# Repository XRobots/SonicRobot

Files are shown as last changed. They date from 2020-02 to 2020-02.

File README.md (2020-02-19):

# SonicRobot

Code and CAD for my two-wheel balancing robot:  https://www.youtube.com/playlist?list=PLpwJoq86vov_tZ3rsMCH5sylqGT5s9TcU

Main parts in the robot are (more details in part 2 of the video series).

-Teensy 3.6 for the main processor.

-MPU6050 on a GY521 style breakout.

-2x Teensy 3.2 to read the load cells in the legs.

-2x 20Kg Loadcells.

-2x Sparkfun Qwiic Scales: https://www.sparkfun.com/products/15242 .

-'SN65HVD230 CAN BusBoard Network Transceiver Module compatible with PCA82C250' CAN Bus Trancievers.

-2x ODrive 3.6 56V version.

-2x 150Kv 6374 ODrive branded brushless motors.

-2x Turnigy SK3 6374 149Kv brushless motors.

-4x 8192 CPR encoders also availabe from ODrive.

-Some switches etc to initialise the Odrives and an Estop which brings the ODrive RST pins to ground.

-NRF24L01 Rf device.

-Varios proto board.

Main parts in the remote are:

-Arduino MEGA2650.

-Another NRF24L01 RF device.

-some switches, and some 3-axis joysticks I got from eBay.

Other mechanical parts (check part 1 for  more details):

-2x Wheel drive belts - 450mm AT5 belts.

-2x Wheel drive motor pulleys - 14 tooth AT5 aluminium pulleys, 8mm bore to match the motors.

-2x 200mm SFU1605 ball screws

-2x 10mm-10mm CNC couplers

-8x CNC style V-Wheels, 5mm ID bearings, plus nuts and bolts.

-4x M10/10mm Rose joints.

-A bunch of 2040 and 2020 Vslot extrusion - refer to the CAD and video.

-Misc T-nuts and M4 bolts of various lengths.

-8x 12mm ID / 32mm OD / 10mm thick bearings for hip joints.

-8x 8mm ID / 22mm OD / 7mm thick bearings for knee joints.

-Various lengths of M12 and M10 studding plus washers and nuts to suit.

Other details:

-I'm running it off 2x 6S 5000 mAH LiPo packs in series

-Electronics are on a separate 5v regulator running from a separate 11.1v LiPo battery.

-Put 0.1uF decoupling capacitors on everything.

Main Library Dependencies are:

For Teensy CAN: https://github.com/tonton81/IFCT

For the MPU 6050: https://github.com/jrowberg/i2cdevlib

For the load cells: https://github.com/sparkfun/SparkFun_Qwiic_Scale_NAU7802_Arduino_Library/

For the ODrvies: https://github.com/madcowswe/ODrive/tree/master/Arduino/ODriveArduino

Plus RF24 library from the Arduino libraries manager, other built in libraries

Use the IMUzero example included with the MPU6050 to read the IMU calibration setting and put those into your sketch: https://github.com/jrowberg/i2cdevlib/tree/master/Arduino/MPU6050/examples/IMU_Zero

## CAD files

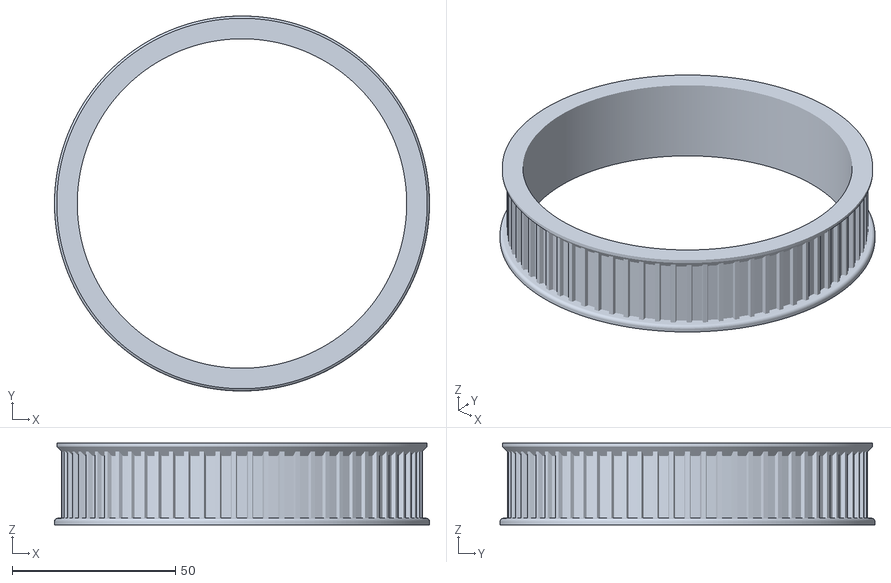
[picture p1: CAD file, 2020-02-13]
CAD/WheelPulley.stl
115.0 x 115.0 x 25.0

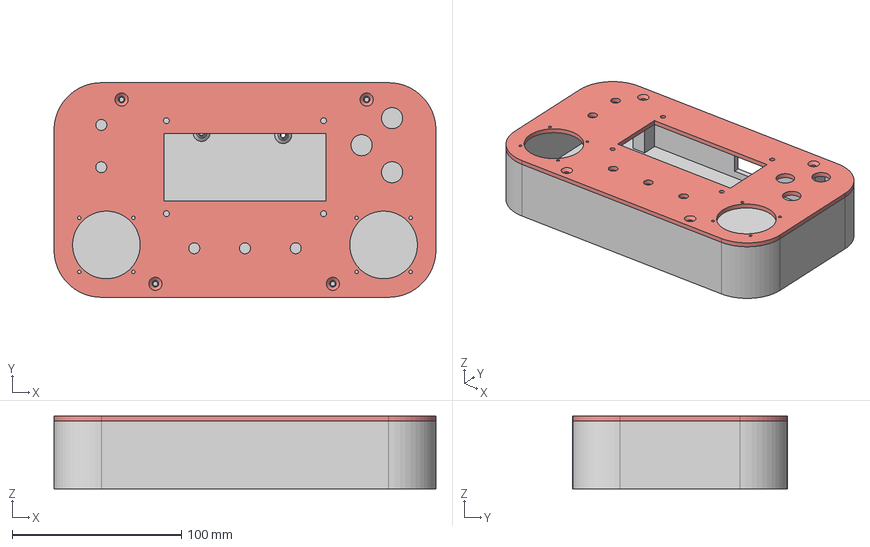
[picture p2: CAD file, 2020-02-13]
CAD/Remote.stp
226.0 x 127.0 x 43.0 mm

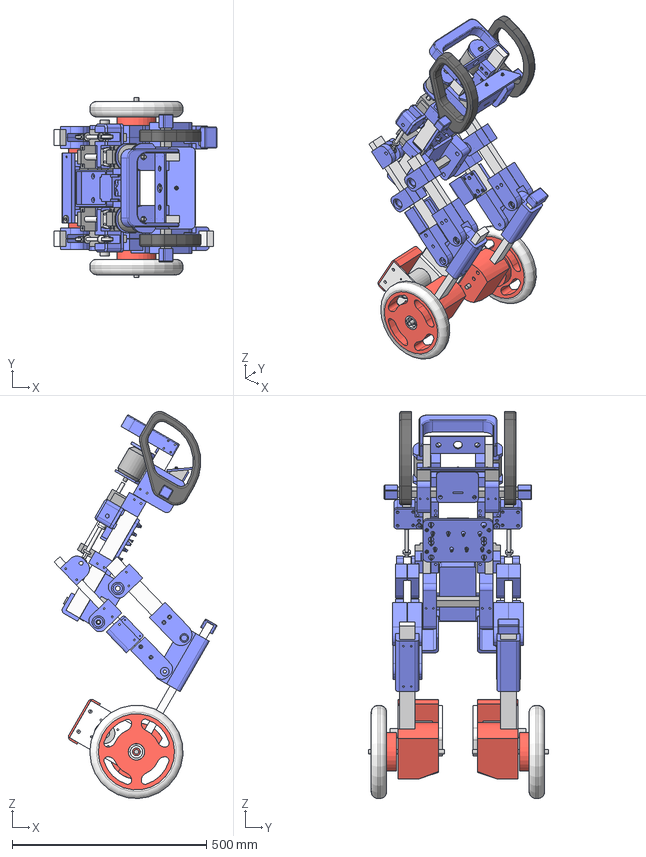
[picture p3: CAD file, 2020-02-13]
CAD/Sonic05.stp
418.0 x 463.0 x 995.0 mm
shin
thigh (1)
thigh (1) (1)
shin(Mirror)
thigh (1)(Mirror)
thigh (1) (1)(Mirror)
ballNut
ballNut (1)
rosejoint(Mirror)
rosejoint(Mirror)(Mirror)

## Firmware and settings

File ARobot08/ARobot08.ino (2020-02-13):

#include <SPI.h>
#include <nRF24L01.h>
#include <RF24.h>
#include <PID_v1.h>  //PID loop from http://playground.arduino.cc/Code/PIDLibrary
#include <Servo.h>
#include <IFCT.h>

Servo servo1;
Servo servo2;

double Pk1 = 7500;          // balancing PID
double Ik1 = 75000;
double Dk1 = 180;

double Setpoint1, Input1, Output1;    // PID variables
PID PID1(&Input1, &Output1, &Setpoint1, Pk1, Ik1 , Dk1, DIRECT);    // PID Setup - balancing IMU

double Pk2 = 3;          // Side to Side PID
double Ik2 = 0;
double Dk2 = 0;

double Setpoint2, Input2, Output2;    // PID variables
PID PID2(&Input2, &Output2, &Setpoint2, Pk2, Ik2 , Dk2, DIRECT);    // PID Setup - side to side IMU

double Pk3 = 22;          // load cell PID
double Ik3 = 0;
double Dk3 = 0;

double Setpoint3, Input3, Output3;    // PID variables
PID PID3(&Input3, &Output3, &Setpoint3, Pk3, Ik3 , Dk3, DIRECT);    // PID Setup - load cell 1

double Pk4 = 22;          // load cell PID
double Ik4 = 0;
double Dk4 = 0;

double Setpoint4, Input4, Output4;    // PID variables
PID PID4(&Input4, &Output4, &Setpoint4, Pk4, Ik4 , Dk4, DIRECT);    // PID Setup - loadcell 2

RF24 radio(25, 24); // CE, CSN
const byte addresses[][6] = {"00001", "00002"};

#include "I2Cdev.h"
#include "MPU6050_6Axis_MotionApps20.h"
#include "Wire.h"
#include <ODriveArduino.h>

// Printing with stream operator
template<class T> inline Print& operator <<(Print &obj,     T arg) { obj.print(arg);    return obj; }
template<>        inline Print& operator <<(Print &obj, float arg) { obj.print(arg, 4); return obj; }

//ODrive Object
ODriveArduino odrive(Serial2);
ODriveArduino odrive2(Serial3);

//**************remote control****************
struct RECEIVE_DATA_STRUCTURE{
  //put your variable definitions here for the data you want to send
  //THIS MUST BE EXACTLY THE SAME ON THE OTHER ARDUINO 

    int16_t menuDown;      
    int16_t Select; 
    int16_t menuUp;  
    int16_t toggleBottom;  
    int16_t toggleTop; 
    int16_t toggle1; 
    int16_t toggle2; 
    int16_t mode;  
    int16_t RLR;
    int16_t RFB;
    int16_t RT;
    int16_t LLR;
    int16_t LFB;
    int16_t LT;
    int16_t checkit;
    int16_t checkit2;

};

int stickRFB;
int stickRLR;
int stickLLR;
int toggleTop;
int toggleBottom;

RECEIVE_DATA_STRUCTURE mydata_remote;

int requested_state;   

// class default I2C address is 0x68
// specific I2C addresses may be passed as a parameter here
// AD0 low = 0x68 (default for SparkFun breakout and InvenSense evaluation board)
// AD0 high = 0x69
MPU6050 mpu;
//MPU6050 mpu(0x69); // <-- use for AD0 high

#define LED_PIN 13 // (Arduino is 11, Teensy is 11, Teensy++ is 6)
bool blinkState = false;

// MPU control/status vars
bool dmpReady = false;  // set true if DMP init was successful
uint8_t mpuIntStatus;   // holds actual interrupt status byte from MPU
uint8_t devStatus;      // return status after each device operation (0 = success, !0 = error)
uint16_t packetSize;    // expected DMP packet size (default is 42 bytes)
uint16_t fifoCount;     // count of all bytes currently in FIFO
uint8_t fifoBuffer[64]; // FIFO storage buffer

// orientation/motion vars
Quaternion q;           // [w, x, y, z]         quaternion container
VectorInt16 aa;         // [x, y, z]            accel sensor measurements
VectorInt16 aaReal;     // [x, y, z]            gravity-free accel sensor measurements
VectorInt16 aaWorld;    // [x, y, z]            world-frame accel sensor measurements
VectorFloat gravity;    // [x, y, z]            gravity vector
float euler[3];         // [psi, theta, phi]    Euler angle container
float ypr[3];           // [yaw, pitch, roll]   yaw/pitch/roll container and gravity vector


float pitch;
float roll;
long velocity;

int menuFlag = 0;
float SetpointTrim1 = 0;

float accum = 0;
float accum2 = 0;
float outputDiv;

float trimPot;
float trimAngle;

float RFB;
int RLR;
int LT;
int LLR;

long drive1;
long drive2;

int switch1;
int switch2;

int toggle1;
int toggle2;

float leg1Dyn;
float leg2Dyn;
float leg1;
float leg2;
float leg1Filtered;
float leg2Filtered;

float leg3;
float leg4;
float leg3Filtered;
float leg4Filtered;

float leg1Output;
float leg2Output;

float legs;
float legs2;

float arm1;
float arm2;

float arm1Filtered;
float arm2Filtered;

unsigned long currentMillis;

long previousMillis = 0;    // set up timers
long interval = 10;        // time constant for timers
unsigned long count;

int loopTime;
int previousLooptime;

unsigned long previousSafetyMillis;

int IMUdataReady = 0;
volatile bool mpuInterrupt = false;     // indicates whether MPU interrupt pin has gone high

int bitVar1;    // CAN bus receive
int bitVar2;
int bitVar1Z = 0;    // CAN bus receive
int bitVar2Z = 0;

// ****************** SETUP ******************************

void setup() {

    // radio stuff

    radio.begin();
    radio.openWritingPipe(addresses[0]); // 00002
    radio.openReadingPipe(1, addresses[1]); // 00001
    radio.setPALevel(RF24_PA_MIN);

    radio.startListening();
    
    // join I2C bus (I2Cdev library doesn't do this automatically)
    #if I2CDEV_IMPLEMENTATION == I2CDEV_ARDUINO_WIRE
        Wire.begin();
        Wire.setClock(100000); // 400kHz I2C clock. Comment this line if having compilation difficulties
    #elif I2CDEV_IMPLEMENTATION == I2CDEV_BUILTIN_FASTWIRE
        Fastwire::setup(400, true);
    #endif

    // initialize serial communication
    Serial.begin(115200);

    //ODrive serial port
    Serial2.begin(115200);
    Serial3.begin(115200);

    // initialize IMU 
    mpu.initialize();
    devStatus = mpu.dmpInitialize();

    // supply your own gyro offsets here, scaled for min sensitivity
    mpu.setXGyroOffset(176);
    mpu.setYGyroOffset(-31);
    mpu.setZGyroOffset(57);
    mpu.setXAccelOffset(-2424);
    mpu.setYAccelOffset(272);
    mpu.setZAccelOffset(987);

    // make sure it worked (returns 0 if so)
    if (devStatus == 0) {
        // turn on the DMP, now that it's ready
        mpu.setDMPEnabled(true);

        // enable Arduino interrupt detection
        attachInterrupt(0, dmpDataReady, RISING);
        mpuIntStatus = mpu.getIntStatus();

        // get expected DMP packet size for later comparison
        packetSize = mpu.dmpGetFIFOPacketSize();
    } else {
        // ERROR!
        // 1 = initial memory load failed
        // 2 = DMP configuration updates failed
        // (if it's going to break, usually the code will be 1)
        Serial.print(F("DMP Initialization failed (code "));
        Serial.print(devStatus);
        Serial.println(F(")"));
    }

    Can0.setBaudRate(500000);     // CAN Bus device
    Can0.enableFIFO();

    // Setup PID controllers

    PID1.SetMode(AUTOMATIC);              
    PID1.SetOutputLimits(-360000, 360000);
    PID1.SetSampleTime(10);

    PID2.SetMode(AUTOMATIC);              
    PID2.SetOutputLimits(-120000, 120000);
    PID2.SetSampleTime(10);

    PID3.SetMode(AUTOMATIC);              
    PID3.SetOutputLimits(-80000, 80000);
    PID3.SetSampleTime(10);

    PID4.SetMode(AUTOMATIC);              
    PID4.SetOutputLimits(-80000, 80000);
    PID4.SetSampleTime(10);

    //switch inputs 
    
    pinMode(22, INPUT_PULLUP);
    pinMode(23, INPUT_PULLUP);

    servo1.attach(26);    // arm servos 
    servo2.attach(27);
    servo1.write(90);     // default positons
    servo2.write(90);

}

// ********************* MAIN LOOP *******************************

void loop() {  

        CAN_message_t msg;
        if ( Can0.read(msg) ) canSniff(msg);
      
        currentMillis = millis();
        if (currentMillis - previousMillis >= 10) {  // start timed event
          
        previousMillis = currentMillis; 

        // measure loop time / optional

        loopTime = currentMillis - previousLooptime;
        //Serial.print("time: ");
        //Serial.print(loopTime);
        //Serial.print("\t");
        previousLooptime = currentMillis;    

        // receive readio data
        
        if (radio.available()) {
                    radio.read(&mydata_remote, sizeof(RECEIVE_DATA_STRUCTURE));
                    previousSafetyMillis = currentMillis; 
        }

        // check for dodgy radio issues

        if (mydata_remote.checkit == 1 && mydata_remote.checkit2 == 100) { 

            stickLLR = mydata_remote.LLR;
            stickRFB = mydata_remote.RFB;
            stickRLR = mydata_remote.RLR;
            toggleTop = mydata_remote.toggleTop;
            toggleBottom = mydata_remote.toggleBottom;
            toggle1 = mydata_remote.toggle1;
            toggle2 = mydata_remote.toggle2;
        }

       // check if remote has become disconnected

        if(currentMillis - previousSafetyMillis > 200) {         
            Serial.println("*no data* ");
            stickRLR = 512;
            stickRFB = 512;
            stickLLR = 512;
        }    

        // read switches

        switch1 = digitalRead(22);    // init
        switch2 = digitalRead(23);    // init2


        // init ODrives

        if (switch1 == 0) {     // init Odrive
            OdriveInit();
        }

        if (switch2 == 0) {     // init Odrive
            OdriveInit2();
        }

        // deal with remote scaling

        RFB = map(stickRFB,0,1023,1023,0);   
        LLR = map(stickLLR,0,1023,1023,0);   

        RFB = (float) (RFB - 512) / 120;
        LLR = ((LLR - 512)  * 100);

        // threshhold drive stick        

        if (RFB <= 0.25 && RFB >= -0.25) {
            RFB = 0;
        }  

        // digital trim

        if (mydata_remote.menuDown == 1 && menuFlag == 0) {
            SetpointTrim1 = SetpointTrim1 - 0.1;
            menuFlag = 1;
        }

        else if (mydata_remote.menuUp == 1 && menuFlag == 0) {
            SetpointTrim1 = SetpointTrim1 + 0.1;
            menuFlag = 1;
        }

        if (mydata_remote.menuDown == 0 && mydata_remote.menuUp == 0) {
            menuFlag = 0;
        }

        // threshold steering stick

        if (LLR < 5000 && LLR > -5000) {
          LLR = 0;
        }

        if (LLR < -5000) {
          LLR = LLR + 5000;
        }

        else if (LLR > 5000) {
          LLR = LLR - 5000;
        }

        // get two numbers for the two leg actuators

        legs2 = map(stickRLR,0,1023,1023,0);      // right hand stick
        legs2 = ((legs2 - 512)  * 100);

        legs = map(stickLLR,0,1023,1023,0);       // left hand stick
        legs = ((legs - 512)  * 100);

        legs = legs + legs2;                      // sum both

        // threshhold legs sticks
        
        if (legs < 5000 && legs > -5000) {
          legs = 0;
        }

        if (legs < -5000) {
          legs =  legs + 5000;
        }

        else if (legs > 5000) {
          legs = legs - 5000;
        }

        if (toggle2 == 1) {       // use the IMU for stability
            Input2 = roll*3000;
        }

        else if (toggle2 == 0) {       // don't use the IMU for stability
            Input2 = 0;
        }

        if (toggle1 == 1) {       // use the sticks to control the leg actuators
            Setpoint2 = legs;
        }

        else if (toggle1 == 0) {       // don't use the sticks to control the leg actuators
            Setpoint2 = 0;
        }

        
        PID2.Compute();     
        
        // move the legs       

        if (Output2 > 0) {
          leg1 = (Output2);
        }
        else {
          leg1 = 0;
        }
  
        if (Output2 < 0) {
          leg2 = abs(Output2);
        }  
        else {
          leg2 = 0;
        }

        // filter leg motions - manual steering
        
        leg1Filtered = filter(leg1, leg1Filtered, 50);
        leg2Filtered = filter(leg2, leg2Filtered, 50);

        // filter leg motions - loadcells
        
        leg3Filtered = filter(Output3, leg3Filtered, 22);
        leg4Filtered = filter(Output4, leg4Filtered, 22);

        // combine leg data

        if (toggleBottom == 1){     // turn on leg load cell data

            leg1Output = leg1Filtered + leg4Filtered;
            leg2Output = leg2Filtered + leg3Filtered;
        }

        else if (toggleBottom == 0) {   // turn off leg load cell data
          
            leg1Output = leg1Filtered;
            leg2Output = leg2Filtered;
        }        


        // zero CAN bus data when the switch is pressed

        if (mydata_remote.Select == 1) {
          bitVar1Z = bitVar1;
          bitVar2Z = bitVar2;
        }

        // receive CAN data and combines bits

        bitVar1 = bitVar1 - bitVar1Z;
        bitVar2 = bitVar2 - bitVar2Z;

        bitVar1 = constrain(bitVar1,0,8000);
        bitVar2 = constrain(bitVar2,0,8000);

        // leg actuator stuff

        //Setpoint3 = roll * 200;
        //Setpoint4 = roll * -200;

        Setpoint3 = 0;
        Setpoint4 = 0;
        
        Input3 = bitVar1*-1;    // invert data
        Input4 = bitVar2*-1;

        PID3.Compute();
        PID4.Compute();

        // see if IMU data is ready based on the interrupt
          
        if (IMUdataReady == 1) {
          readAngles();             // call the function on the other tab to get the IMU data
        }

        // 'agressive driving' stuff - *****experimental*****

        outputDiv = Output1 / 80000;   // 300000
        accum =  (outputDiv + RFB);
        accum = constrain(accum,-3,3);

        // convert angles to degrees
       
        pitch = (ypr[1] * 180/M_PI);           
        roll = (ypr[2] * 180/M_PI)+2;      

        // balancing PID stuff

        Setpoint1 = RFB + SetpointTrim1 + accum;
        Input1 = pitch;
        PID1.Compute();       

        //steering - differential drive
        
        drive1 = Output1 + LLR;
        drive2 = (Output1*-1) + LLR;  

        // drive ODrives

        if (toggleTop == 1) {     // motor enable
                        
              odrive.SetVelocity(0, drive1); 
              odrive.SetVelocity(1, drive2);
        }

        else if (toggleTop == 0) {     // motor dis-enable

              odrive.SetVelocity(0, 0); 
              odrive.SetVelocity(1, 0);
        }

        leg1Output = constrain(leg1Output, 0,100000);   // make sure we don't run the end stops
        leg2Output = constrain(leg2Output, 0,100000);

        odrive2.SetPosition(1, leg1Output);       // drive leg actuators
        odrive2.SetPosition(0, leg2Output); 

        // drive arm servos

        arm1 = map(stickLLR,0,1023,180,0);
        arm2 = map(stickLLR,0,1023,180,0);

        arm1Filtered = filter(arm1, arm1Filtered, 15);
        arm2Filtered = filter(arm2, arm2Filtered, 15);

        servo1.write(arm1Filtered);
        servo2.write(arm2Filtered);


      }     // end of timed event          
   
}           // end  of main loop


// filter function

float filter(float lengthOrig, float currentValue, int filter) {
  float lengthFiltered =  (lengthOrig + (currentValue * filter)) / (filter + 1);
  return lengthFiltered;  
}

// CAN Bus receive function

void canSniff(const CAN_message_t &msg) {
  //Serial.print(" ID: "); Serial.print(msg.id, HEX);
  //Serial.print(" Buffer: ");
  for ( uint8_t i = 0; i < msg.len; i++ ) {
    //Serial.print(msg.buf[i], DEC); Serial.print(" ");
  }

  if (msg.id == 0x222) {
      bitVar1 = ((msg.buf[1] * 256) + msg.buf[0]*1.5);   // right leg - scale for difference in values
  }
  else if (msg.id == 0x221) {
      bitVar2 = ((msg.buf[1] * 256) + msg.buf[0]*1.5);   // left leg - scale for difference in values
  }
  
}

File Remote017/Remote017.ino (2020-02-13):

#include <SPI.h>
#include <nRF24L01.h>
#include <RF24.h>

#include <Wire.h>  // Comes with Arduino IDE
#include <LiquidCrystal_I2C.h>

// Set the pins on the I2C chip used for LCD connections (Some LCD use Address 0x27 and others use 0x3F):
LiquidCrystal_I2C lcd(0x27,20,4);  // set the LCD address to 0x27 for a 16 chars and 2 line display

unsigned long previousMillis = 0;
const long interval = 20;

int but1;
int but2;
int but3;
int but4;
int but5;

int sw1;
int sw2;
int sw3;

int axis1;
int axis2;
int axis3;
int axis4;
int axis5;
int axis6;

String count;

struct SEND_DATA_STRUCTURE{
//struct __attribute__((__packed__)) SEND_DATA_STRUCTURE{
  //put your variable definitions here for the data you want to send
  //THIS MUST BE EXACTLY THE SAME ON THE OTHER ARDUINO

    int16_t menuDown;  
    int16_t Select;    
    int16_t menuUp;  
    int16_t toggleBottom;  
    int16_t toggleTop; 
    int16_t toggle1;
    int16_t toggle2;
    int16_t mode;  
    int16_t RLR;
    int16_t RFB;
    int16_t RT;
    int16_t LLR;
    int16_t LFB;
    int16_t LT;
    int16_t checkit;
    int16_t checkit2;
};

struct RECEIVE_DATA_STRUCTURE_REMOTE{
  //put your variable definitions here for the data you want to receive
  //THIS MUST BE EXACTLY THE SAME ON THE OTHER ARDUINO
  int16_t mode;
  int16_t count;
};

int remoteFlag = 0;

SEND_DATA_STRUCTURE mydata_send;
RECEIVE_DATA_STRUCTURE_REMOTE mydata_remote;

RF24 radio(7, 8); // CE, CSN
const byte addresses[][6] = {"00001", "00002"};


void setup() {  

  lcd.init();  // initialize the lcd 
  lcd.backlight();

  pinMode(38, INPUT_PULLUP);
  pinMode(40, INPUT_PULLUP);
  pinMode(42, INPUT_PULLUP);
  pinMode(44, INPUT_PULLUP);
  pinMode(46, INPUT_PULLUP);
  
  pinMode(28, INPUT_PULLUP); 
  pinMode(30, INPUT_PULLUP); 
  pinMode(32, INPUT_PULLUP);

  pinMode(A0, INPUT);
  pinMode(A1, INPUT);
  pinMode(A2, INPUT);
  pinMode(A4, INPUT);
  pinMode(A5, INPUT);
  pinMode(A6, INPUT);
  
  radio.begin();
  radio.openWritingPipe(addresses[1]); // 00001
  radio.openReadingPipe(1, addresses[0]); // 00002
  radio.setPALevel(RF24_PA_MIN);

  lcd.begin(20,4);   // Initialize the lcd for 20 chars 4 lines, turn on backlight

  lcd.setCursor(0,0);
  lcd.print("Sonic Remote        ");
  lcd.setCursor(0,1);
  lcd.print("XRobots.co.uk       ");

  Serial.begin(115200);

  mydata_send.checkit = 1;
  mydata_send.checkit2 = 100;
  
    
}

void loop() {

     unsigned long currentMillis = millis();
         if (remoteFlag == 0 && currentMillis - previousMillis >= 10) { 

              but1 =  digitalRead(38);
              but2 =  digitalRead(40);
              but3 =  digitalRead(42);
              but4 =  digitalRead(44);
              but5 =  digitalRead(46);  

              sw1 = digitalRead(28);
              sw2 = digitalRead(30);
              sw3 = digitalRead(32);
                           
              if (but1 == 0) {
                mydata_send.menuDown = 1;
              }
              else {
                mydata_send.menuDown = 0;
              }

              if (but2 == 0) {
                mydata_send.Select = 1;
              }
              else {
                mydata_send.Select = 0;
              }
                            
              if (but3 == 0) {
                mydata_send.menuUp = 1;
              }
              else {
                mydata_send.menuUp = 0;
              }
              
              if (but4 == 0) {
                mydata_send.toggleBottom = 1;
              }
              else {
                mydata_send.toggleBottom = 0;
              }
              
              if (but5 == 0) {
                mydata_send.toggleTop = 1;
              }
              else {
                mydata_send.toggleTop = 0;
              }

              //******************

              if (sw1 == 0) {
                mydata_send.toggle1 = 1;
              }
              else {
                mydata_send.toggle1 = 0;
              }
              
              if (sw2 == 0) {
                mydata_send.toggle2 = 1;
              }
              else {
                mydata_send.toggle2 = 0;
              }
              

              

              
              axis1 = analogRead(A0);
              axis2 = analogRead(A1);
              axis3 = analogRead(A2);
              axis4 = analogRead(A3);
              axis5 = analogRead(A4);
              axis6 = analogRead(A5);
             
              mydata_send.RLR = axis1;
              mydata_send.RFB = axis2;
              mydata_send.RT = axis3;
              mydata_send.LLR = axis4;
              mydata_send.LFB = axis5;
              mydata_send.LT = axis6;   

             
              //delay(5);
              //radio.startListening();              
              //radio.read(&mydata_remote, sizeof(RECEIVE_DATA_STRUCTURE_REMOTE));

              count = String(mydata_remote.count);


              /*
              
              lcd.setCursor(0,3);
              lcd.print(count);
    
              if (mydata_remote.mode == 0) {
                lcd.setCursor(0,0);
                lcd.print("Mode 0 - Safe       ");
                lcd.setCursor(0,1);
                lcd.print("                    ");
              }
              else if (mydata_remote.mode == 1) {
                lcd.setCursor(0,0);
                lcd.print("Mode 1 - Kin Test   ");
                lcd.setCursor(0,1);
                lcd.print("                    ");
              }
              else if (mydata_remote.mode == 2) {
                lcd.setCursor(0,0);
                lcd.print("Mode 2 -            ");
                lcd.setCursor(0,1);
                lcd.print("                    ");
              }
              else if (mydata_remote.mode == 3) {
                lcd.setCursor(0,0);
                lcd.print("Mode 3 -            ");
                lcd.setCursor(0,1);
                lcd.print("                    ");
              }
              else if (mydata_remote.mode == 4) {
                lcd.setCursor(0,0);
                lcd.print("Mode 4 -            ");
                lcd.setCursor(0,1);
                lcd.print("                    ");
              }
              else if (mydata_remote.mode == 5) {
                lcd.setCursor(0,0);
                lcd.print("Mode 5 -            ");
                lcd.setCursor(0,1);
                lcd.print("                    ");
              }

              */

              //radio.stopListening();
              radio.write(&mydata_send, sizeof(SEND_DATA_STRUCTURE));
                
              previousMillis = currentMillis;  
         }        
        


      



  }  // end of main loop

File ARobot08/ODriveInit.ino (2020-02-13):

void OdriveInit() {

      for (int axis = 0; axis < 2; ++axis) {
          Serial2 << "w axis" << axis << ".controller.config.vel_limit " << 360000.0f << '\n';
          Serial2 << "w axis" << axis << ".motor.config.current_lim " << 30.0f << '\n';
          Serial2 << "w axis" << axis << ".motor.config.calibration_current " << 15.0f << '\n';

          //delay(1000);

          requested_state = ODriveArduino::AXIS_STATE_MOTOR_CALIBRATION;
          Serial << "Axis" << axis << ": Requesting state " << requested_state << '\n';
          odrive.run_state(axis, requested_state, true);

          delay(1000);
    
          requested_state = ODriveArduino::AXIS_STATE_ENCODER_OFFSET_CALIBRATION;
          Serial << "Axis" << axis << ": Requesting state " << requested_state << '\n';
          odrive.run_state(axis, requested_state, true);

          delay(1000);
    
          requested_state = ODriveArduino::AXIS_STATE_CLOSED_LOOP_CONTROL;
          Serial << "Axis" << axis << ": Requesting state " << requested_state << '\n';
          odrive.run_state(axis, requested_state, false); // don't wait 
      }       
        
}

void OdriveInit2() {

      for (int axis = 0; axis < 2; ++axis) {
          Serial3 << "w axis" << axis << ".controller.config.vel_limit " << 250000.0f << '\n';
          Serial3 << "w axis" << axis << ".motor.config.current_lim " << 40.0f << '\n';
          Serial3 << "w axis" << axis << ".motor.config.calibration_current " << 15.0f << '\n';

          //delay(1000);

          requested_state = ODriveArduino::AXIS_STATE_MOTOR_CALIBRATION;
          Serial << "Axis" << axis << ": Requesting state " << requested_state << '\n';
          odrive2.run_state(axis, requested_state, true);

          delay(1000);
    
          requested_state = ODriveArduino::AXIS_STATE_ENCODER_OFFSET_CALIBRATION;
          Serial << "Axis" << axis << ": Requesting state " << requested_state << '\n';
          odrive2.run_state(axis, requested_state, true);

          delay(1000);
    
          requested_state = ODriveArduino::AXIS_STATE_CLOSED_LOOP_CONTROL;
          Serial << "Axis" << axis << ": Requesting state " << requested_state << '\n';
          odrive2.run_state(axis, requested_state, false); // don't wait 
      }       
        
}
